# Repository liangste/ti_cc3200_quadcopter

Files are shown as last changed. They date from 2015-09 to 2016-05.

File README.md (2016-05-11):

# cc3200 quadcopter
a small quadcopter based on TI [CC3200](http://www.ti.com/product/cc3200) Wifi Processor

This is a project I started to develop a small quadcopter that I can control through my smartphone. It began as the idea: "wouldn't it be cool to fly a quadcopter with my phone?". Soon after, I got a development board for the CC3200 platform and I enrolled on a year-long journey of hw/sw development.

#Connecting to Smartphone
Connecting to Smartphone (https://youtu.be/c3Ppp-kUkaQ)

#Flight Video
Flight Video (https://youtu.be/NUO0UMu_Gpo)

Most "control" related components are routed to the top of the PCB. The board measure 4cm x 4cm and contains 4 copper layers.

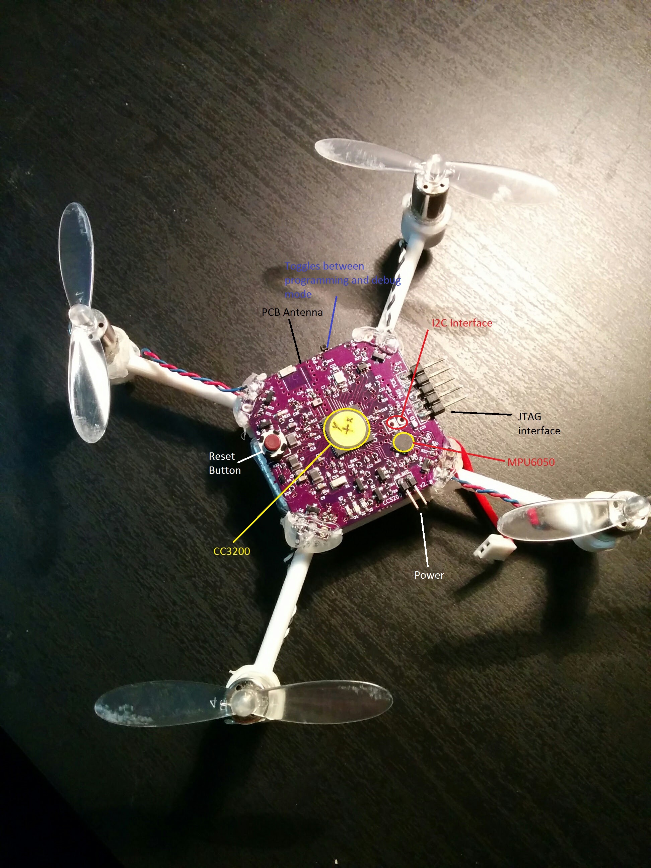
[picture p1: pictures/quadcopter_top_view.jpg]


While "Power" related components are routed to the bottom. Note that there are 4 MOSFETs placed in each corner, one for each DC motors.

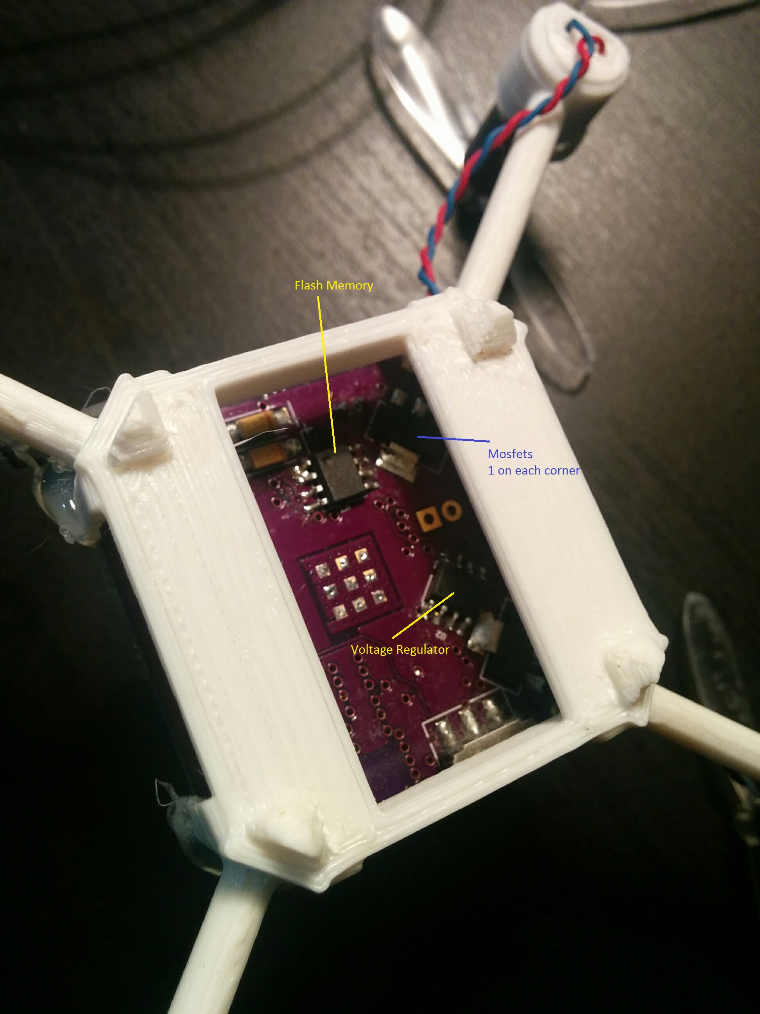
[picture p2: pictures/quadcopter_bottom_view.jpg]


While developing the sw, I also made a simple PyQt app for visualizing the measured and calculated sensor readings from the quadcopter. This "tester" app, as I call it, was important for developing Kalman filter for accelerometer and gyroscope readings.

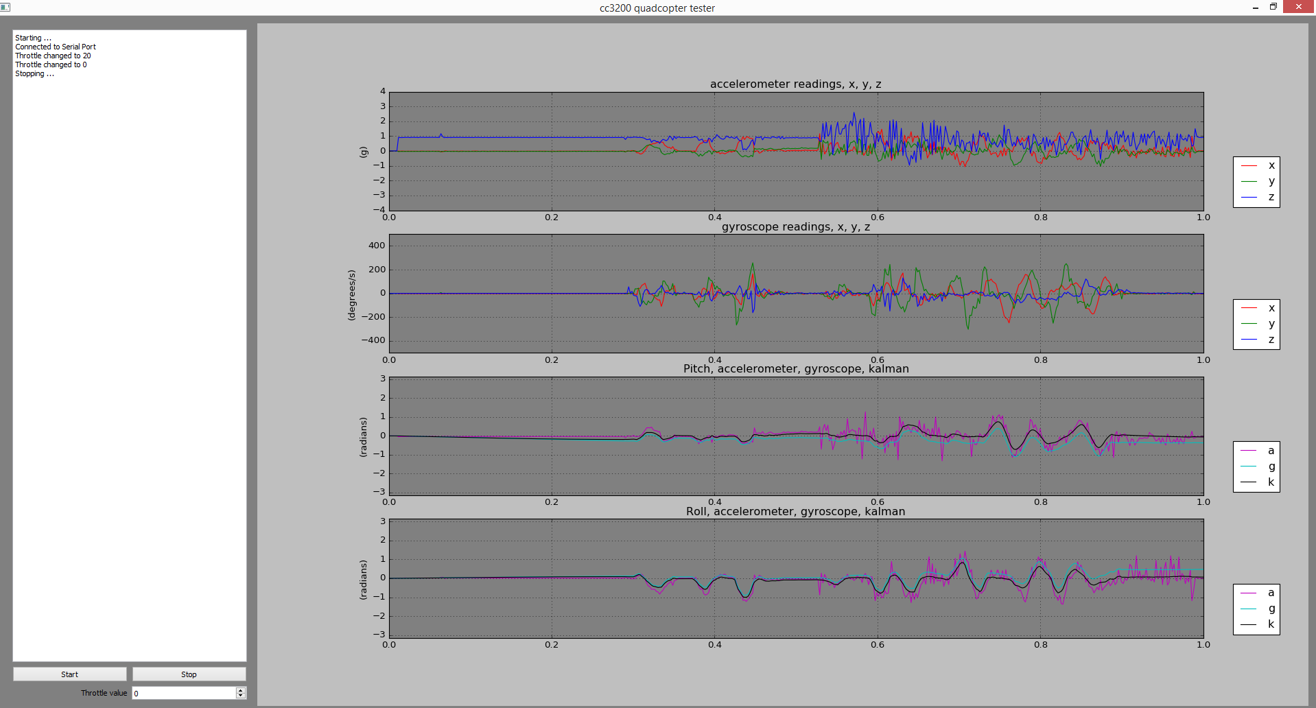
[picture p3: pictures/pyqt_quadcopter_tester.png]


Here's picture showing the "evolution" of this quadcopter. On the left we have the original CC3200 development board, on which my board designs were based. In the middle is the first version of the PCB. It was functional, but had several shortcomings that motivated me to develop another version. On the right, you see the final version with much smaller PCB mounted on a chasis that I made on SolidWorks and printed out using a local 3D printer.

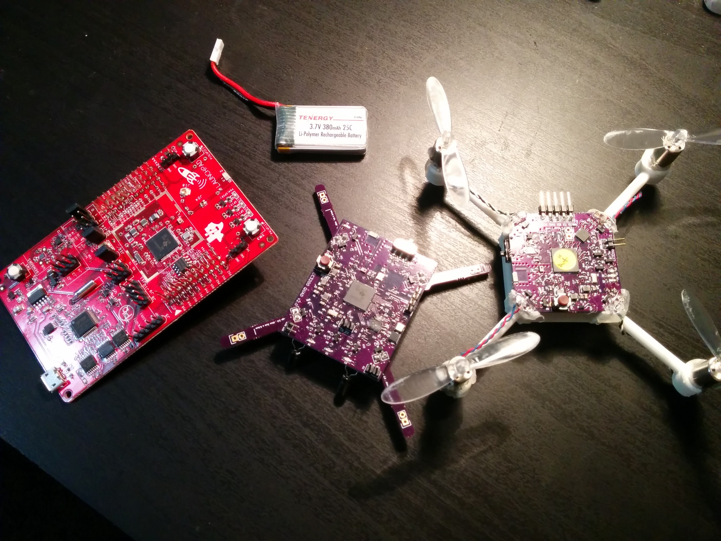
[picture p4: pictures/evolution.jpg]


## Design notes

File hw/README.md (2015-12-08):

# Hardware Overview

Photo Gallery [here](https://goo.gl/photos/aTtyzAjJARxAQHJD8)

## Introduction

The hardware is designed using [KiCAD](http://kicad-pcb.org/) and manufactured with [OSI Park](https://oshpark.com/) PCB manufacturing facility. Build version for the KiCAD used is 2014-12-04 bZR 5312.

[CC3200](http://www.ti.com/product/cc3200) is a Wifi-based microcontroller made by Texas Instruments. For this project, CC3200 is used as the processor as well as communication interface. The chip runs at 80MHz and has an embedded Wifi co-processor that I can link with and control using my smartphone. I used this chip because 1) it's not too expensive, 2) its suitable for a 4-layer design, which is the current maximum amount of layers for OSH Park and 3) because it has a Wifi co-processor in the same die.

## Hardware Breakdown

### Wifi processor

VQFN-64 package in a 9mm x 9mm package. Contains GPIO, UART, I2C, SPI, PWM, and Parallel Camera interface.

### Power

Main power source for the quad is a 3.7V Li-Po battery. The voltaged is stepped-down to 3.3V using Low-DropOut (LDO) regulators.

### Motor Control

4 MOSFETs are used to control 4 DC motors. GPIO_9, 10, 11, and 28 provide the PWM signals from CC3200.

### Acceleromter + Gyro

MPU6050 is an Gyroscope + Accelerometer 2 in 1 sensor with I2C and SPI interfaces. One nice thing about the MPU6050 is the Low-Pass Filter which can be used to filter out unwanted Acceleromter high-frequency noise caused by motor vibrations.

### Indicator LEDs

3 LEDs indicate Wifi-connectivity status, Sensor status and transmission indications. 1 Red LED is used to indicate power status.

## Build and Test

Once schematics and layouts of the board is done. The design is sent to OSH Park for processing. Turnaround time was usually 2 weeks for 2 layers boards and 3-4 weeks for 4 layer boards. Once the board arrives, I picked them up and soldered with components that I ordered separately from Digikey. I constructed a ControLeo2-based reflow oven from [Whizoo](http://www.whizoo.com/) and used it to solder SMD components on the top of the board. The bottom is left for larger components like MOSFETS, NAND memory and LDO regulators that I can solder by hand.

I used the following chart as a guide for testing each hardware components. The rows go from easiest to hardest to verify.

| Component | How to test |
| :--- | :---: |
|CC3200 Power|Is the Red Power LED on? Probe at 3.3V|
|JTAG| Use CCS to connect to CC3200 using TCK and TMS lines |
|Flash Programming| Use Tx and Rx lines to flash binaries to NAND using UniFlash |
|UART|Print out characters and receive characters from the terminal. If Flash Programming work, this should also work|
|LEDs|Blink LEDs in a sequence|
|PMW|Make sure that varying PWM duty cycle changes motor speed|
|I2C|Do a read-write-read test to scrach-pad register on MPU6050. Also test by reading its signature register|
|RF|Start a SimpleLink TCP Server and perform a packet transmission test with smartphone|

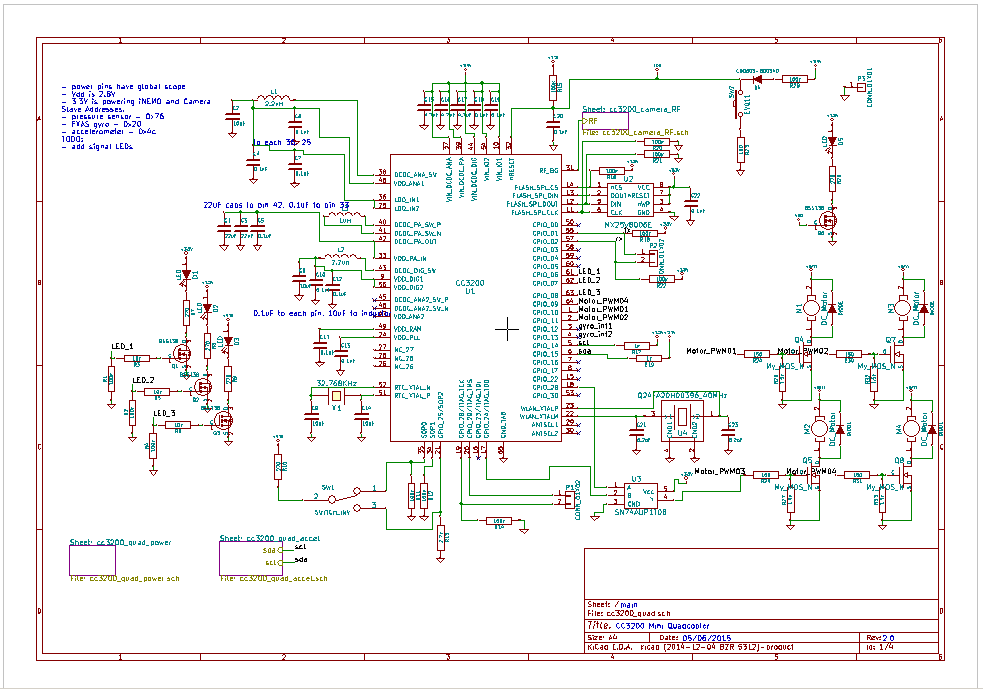
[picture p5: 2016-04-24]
pictures/schematic.png

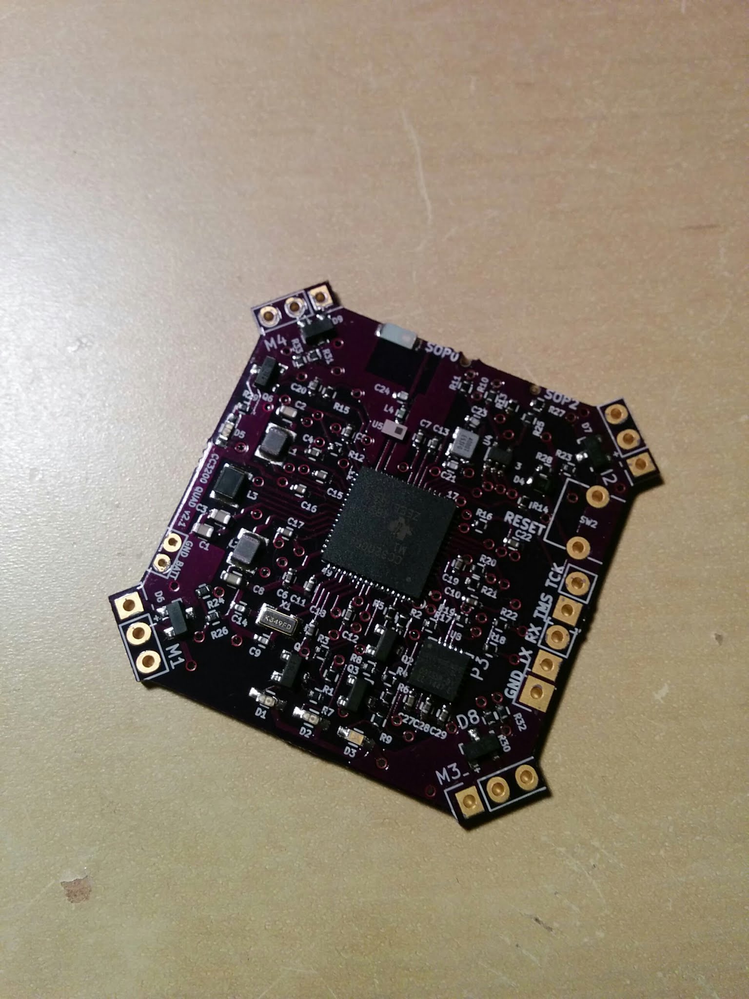
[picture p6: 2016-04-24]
pictures/after_reflow.jpg

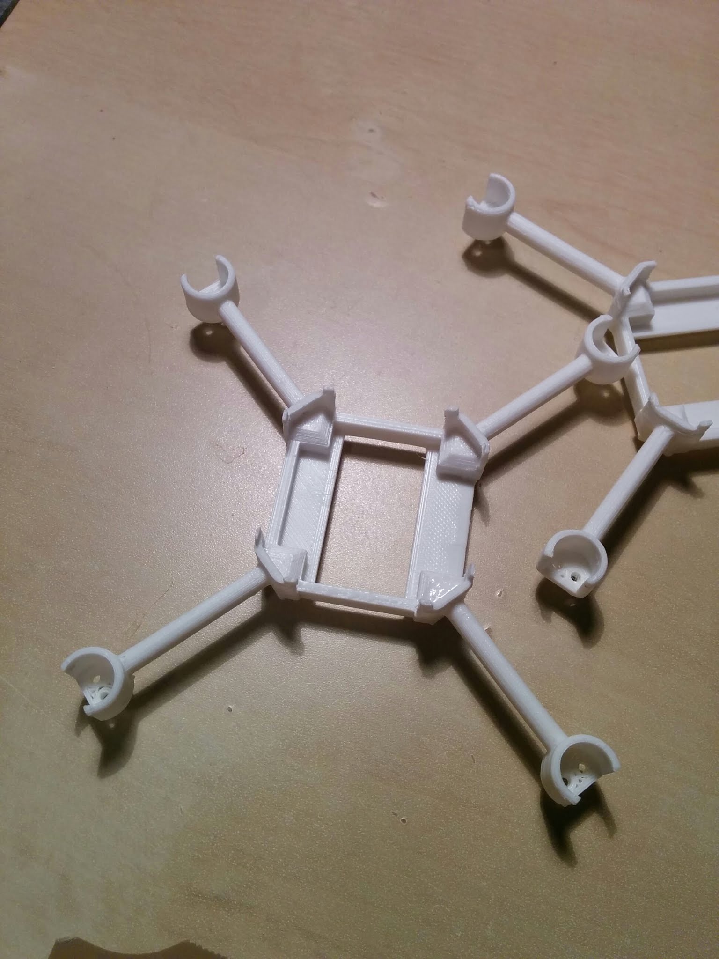
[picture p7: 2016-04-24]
pictures/quadcopter_body.jpg

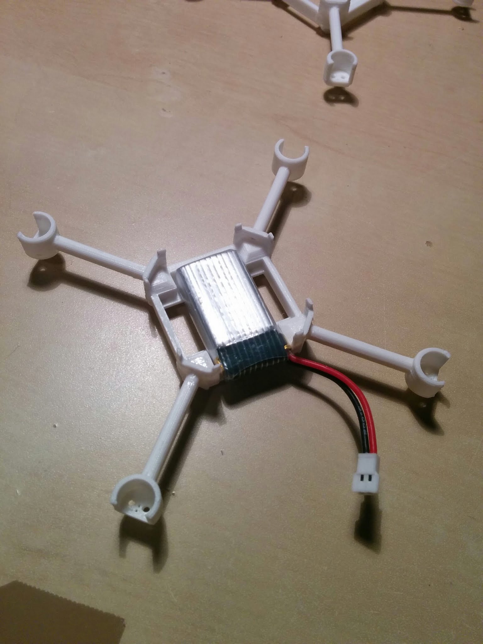
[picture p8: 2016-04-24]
pictures/quadcopter_battery_spacing.jpg

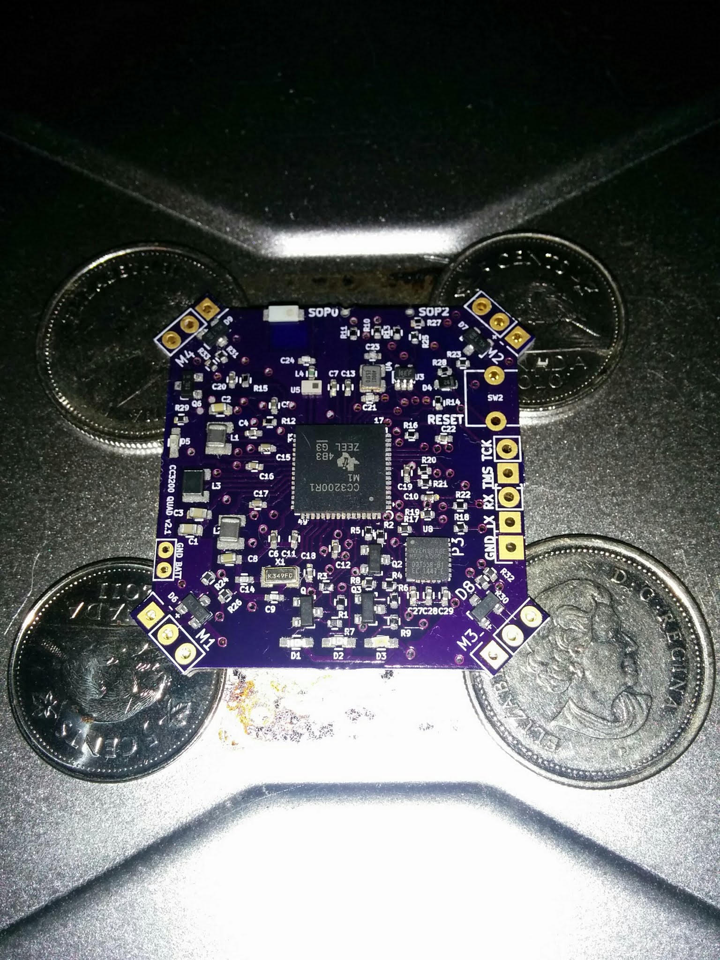
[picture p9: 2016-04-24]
pictures/reflowing.jpg

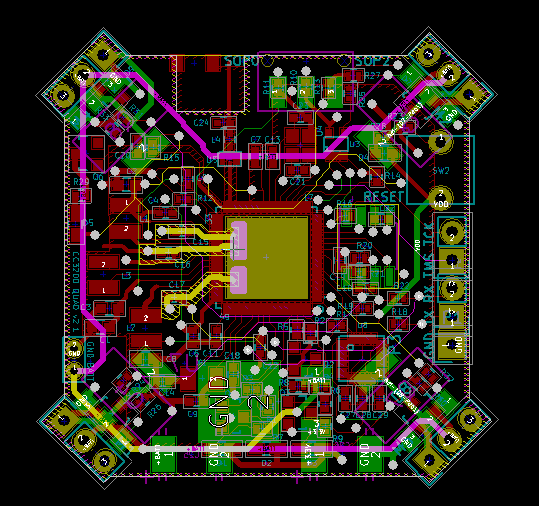
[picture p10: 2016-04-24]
pictures/pcb_layout.png

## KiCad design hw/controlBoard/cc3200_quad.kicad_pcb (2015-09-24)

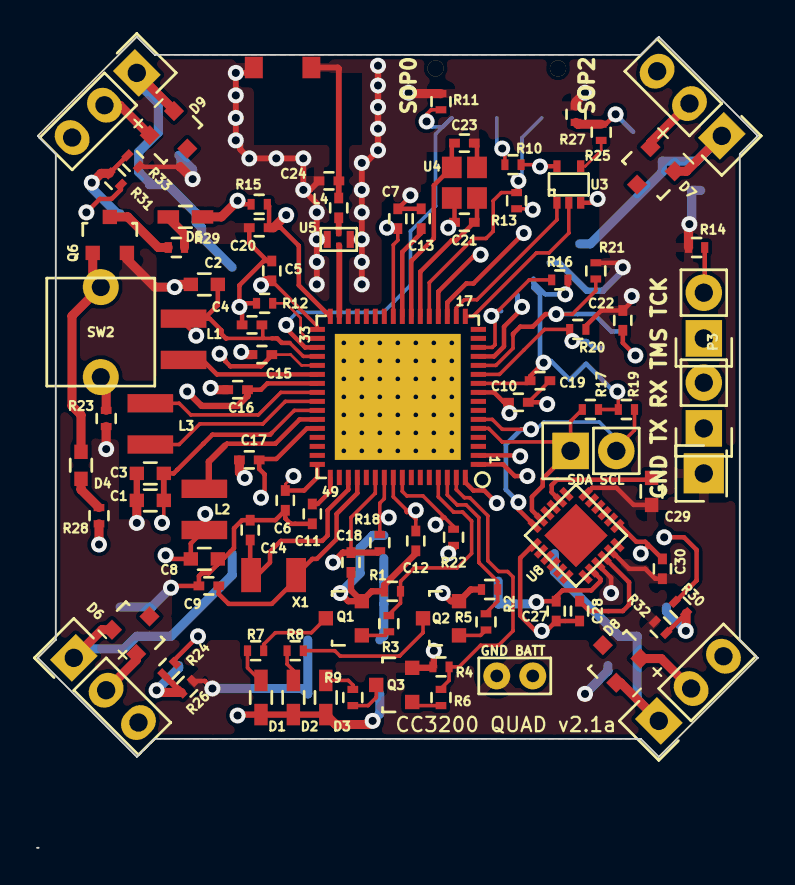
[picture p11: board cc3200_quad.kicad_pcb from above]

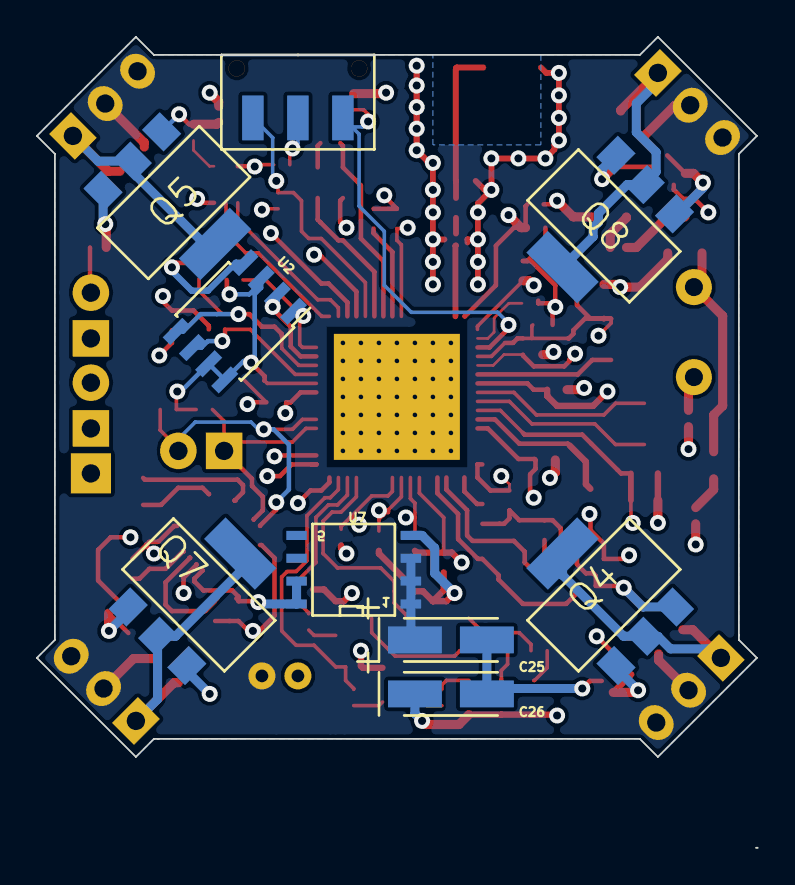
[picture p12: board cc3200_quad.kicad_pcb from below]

Board: 4 copper layers, 40.0 x 40.0 mm, 104 parts (9 on the bottom side), 65 nets.

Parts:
BT1: JST_CONNECTOR; JST_2PIN_2mm
C1, C3: 22uF; C_0603
C2, C8: 10uF; C_0603
C4, C5, C6, C7, C10, C11, C12, C13, C18, C19, C20, C22, C28, C30: 0.1uF; C_0402
C9, C14: 10pF; C_0402
C15, C16, C17: 4.7uF; C_0402
C21, C23: 6.2pF; C_0402
C24: 1.0pF; C_0402
C25, C26: 100uF; TantalC_SizeA_EIA-3216_HandSoldering
C27: 10nF; C_0402
C29: 2.2nF; C_0603
D1, D2, D3, D5: LED; C_0603_HandSoldering
D4: CD0603-B00340; C_0603
D6, D7, D8, D9: BAT54; SOT-23
L1, L2: 2.2uH; Neosid_Inductor_SM-NE29_SMD1008
L3: 1uH; Neosid_Inductor_SM-NE29_SMD1008
L4: 3.6nH; C_0402
M1, M2, M3, M4: DC_Motor; Pin_Header_Straight_1x03
P1, P2, P3: CONN_01X02; Pin_Header_Straight_1x02
P4: CONN_01X01; Pin_Header_Straight_1x01
Q1, Q2, Q3, Q6: BSS138; SOT-23
Q4, Q5, Q7, Q8: BUK9832; SOT-223
R1, R2, R4, R11, R12, R14, R15, R16, R18, R20, R21, R22, R28: 100k; R_0402
R3, R5, R6: 10k; R_0402
R7, R8, R9, R10, R29: 270; R_0402
R13: 2.7k; R_0402
R17, R19: 1k; R_0402
R23: 100; R_0402
R24, R25, R30, R31: 150; R_0402
R26, R27, R32, R33: 1.5k; R_0402
SW1: SWITCH_INV; JS102011SAQN
SW2: EVQ11; EVQ11_Push_Switch
U1: CC3200; cc3200
U2: MX25V8006E; SOIC-8_3.9x4.9mm_Pitch1.27mm
U3: SN74AUP1T08; sc70-5
U4: Q24FA20H00396_40MHz; Q24FA20H
U5: DEA202450BT-1294C1-H; DEA202450BT
U6: AH316M245001; AH316M
U7: MCP1726; SOIC-8-N
U8: MPU6050; MPU-6050
X1: 32.768KHz; ABS07

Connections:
+3.3V: C15.1, C16.1, C17.1, C18.1, C19.1, C22.1, C26.1, C27.1, C30.1, D1.1, D2.1, D3.1, D5.1, R10.1, R15.1, R16.1, R17.1, R18.1, R19.1, R22.1, R28.1, U1.10, U1.37, U1.39, U1.44, U1.54, U2.3, U2.7, U2.8, U3.5, U7.7, U7.8, U8.8, U8.13
+BATT: BT1.1, C25.1, D6.2, D7.2, D8.2, D9.2, M1.2, M2.2, M3.2, M4.2, U7.1, U7.2, U7.3
/LED_1: R1.2, R3.2, U1.61
/LED_2: R2.2, R5.2, U1.62
/LED_3: R4.2, R6.2, U1.63
/Motor_PWM01: R24.2, U1.1
/Motor_PWM02: R30.2, U1.2
/Motor_PWM03: R25.2, U3.4
/Motor_PWM04: R31.2, U1.64
/cc3200_camera_RF/RF: U1.31, U5.1
/cc3200_quad_accel/SCL: P1.1, R17.2, U1.5, U8.23
/cc3200_quad_accel/SDA: P1.2, R19.2, U1.6, U8.24
/rx: P3.2, R22.2, U1.57
/tx: P3.1, R18.2, U1.55
/~Reset: C20.1, D4.2, Q6.1, R15.2, SW2.2, U1.32
GND: BT1.2, C1.2, C2.2, C3.2, C4.2, C5.2, C6.2, C7.2, C8.2, C9.2, C10.2, C11.2, C12.2, C13.2, C14.2, C15.2, C16.2, C17.2, C18.2, C19.2, C20.2, C21.2, C22.2, C23.2, C24.1, C24.2, C25.2, C26.2, C27.2, C28.2, C29.1, C30.2, L4.2, P4.1, Q1.2, Q2.2, Q3.2, Q4.3, Q5.3, Q6.2, Q7.3, Q8.3, R1.1, R2.1, R4.1, R11.2, R12.2, R13.2, R14.1, R20.1, R21.1, R23.2, R26.1, R27.1, R32.1, R33.1, U1.65, U2.4, U3.3, U4.2, U4.4, U5.2, U5.4, U6.1, U6.2, U7.4, U8.1, U8.9, U8.11, U8.18
unnamed: C1.1, C3.1, C5.1, U1.33, U1.42
unnamed: C2.1, C4.1, C6.1, C7.1, L1.1, U1.25, U1.36, U1.48
unnamed: C9.1, U1.52, X1.2
unnamed: C8.1, C10.1, C12.1, L2.1, U1.9, U1.56
unnamed: C11.1, U1.49
unnamed: C13.1, U1.24
unnamed: C14.1, U1.51, X1.1
unnamed: C21.1, U1.22, U4.3
unnamed: C23.1, U1.23, U4.1
unnamed: C28.1, U8.10
unnamed: C29.2, U8.20
unnamed: D1.2, R7.1
unnamed: D2.2, R8.1
unnamed: D3.2, R9.1
unnamed: D4.1, R28.2
unnamed: D5.2, R29.1
unnamed: D6.1, M1.1, Q4.2
unnamed: D7.1, M2.1, Q5.2
unnamed: D8.1, M3.1, Q7.2
unnamed: D9.1, M4.1, Q8.2
unnamed: L1.2, U1.38
unnamed: L2.2, U1.43
unnamed: L3.1, U1.41
unnamed: L3.2, U1.40
unnamed: L4.1, U5.3
unnamed: P2.1, U1.20
unnamed: P2.2, R14.2, U1.19
unnamed: Q1.1, R3.1
unnamed: Q1.3, R7.2
unnamed: Q2.1, R5.1
unnamed: Q2.3, R8.2
unnamed: Q3.1, R6.1
unnamed: Q3.3, R9.2
unnamed: Q4.1, R24.1, R26.2
unnamed: Q5.1, R25.1, R27.2
unnamed: Q6.3, R29.2
unnamed: Q7.1, R30.1, R32.2
unnamed: Q8.1, R31.1, R33.2
unnamed: R10.2, SW1.2
unnamed: R11.1, SW1.1, U1.35
unnamed: R12.1, U1.34
unnamed: R13.1, SW1.3, U1.21
unnamed: R16.2, U1.14, U2.1
unnamed: R20.2, U1.11, U2.6
unnamed: R21.2, U1.12, U2.5
unnamed: R23.1, SW2.1
unnamed: U1.13, U2.2
unnamed: U1.17, U3.2
unnamed: U1.18, U3.1

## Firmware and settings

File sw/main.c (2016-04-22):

#include "config.h"

#define OSI_STACK_SIZE          524    // stack size in number of *words*
#define mainDELAY_LOOP_COUNT    100000

int init_status;
extern bool g_wifiConnected;
extern bool g_wifiDataAvailable;

extern void(* const g_pfnVectors[])(void);

static void board_init(void);

void vAssertCalled(const char *pcFile, unsigned long ulLine) {
		LOOP_FOREVER();
}

void vApplicationIdleHook(void) {
}

void vApplicationMallocFailedHook(void) {
		UART_PRINT("[Error] FreeRTOS malloc failed\r\n");
		LOOP_FOREVER();
}

void vApplicationStackOverflowHook(OsiTaskHandle *pxTask,
				signed char *pcTaskName) {
		UART_PRINT("[Error] FreeRTOS stack overflow\r\n");
		LOOP_FOREVER();
}

static void board_init(void) {
		MAP_IntVTableBaseSet((unsigned long)&g_pfnVectors[0]);

		MAP_IntMasterEnable();
		MAP_IntEnable(FAULT_SYSTICK);

		PRCMCC3200MCUInit();
}

// ORANGE Blinking LED
void WifiIndicatorTask(void *pvParameters) {
		while(1)
		{
				wifi_indicator_ticks++;
				if (g_wifiInitialized)
				{
						if (g_wifiConnected)
								led_set(ORANGE);
						else
								led_toggle(ORANGE);
				}
				vTaskDelay(100);
		}
}

// GREEN Blinking LED
void SensorIndicatorTask(void *pvParameters) {
		while(1)
		{
				/*
				sensor_indicator_ticks++;
				if (g_sensorInitialized)
				{
						if (g_sensorConnected)
								led_toggle(GREEN);
						g_sensorConnected = 0;
				}
				*/
				vTaskDelay(1000);
		}
}

// BLUE Blinking LED
void CommIndicatorTask(void *pvParameters) {
		while(1)
		{
				comm_indicator_ticks++;
				if (g_wifiConnected) {
						led_toggle(BLUE);
						g_wifiConnected = 0;
				}
				else
						led_clear(BLUE);
				vTaskDelay(40);
		}
}

int main()
{
		board_init();
		pinmux_config();
		InitTerm();

		UART_PRINT("========================================\r\n");
		UART_PRINT("   Initializing CC3200 Quad Firmware\r\n");
		UART_PRINT("========================================\r\n");

		init_status = 0;
		g_wifiConnected = false;
		motors_init();
		led_init();
		if (!mpu6050_init(&init_status)) {
			FAIL("Failed to initialize MPU 6050 Sensor");
			goto LOOP_FOREVER;
		}

		wifiDataLock = xSemaphoreCreateMutex();
		g_wifiDataAvailable = false;

		VStartSimpleLinkSpawnTask(SPAWN_TASK_PRIORITY);

		//xTaskCreate(SerialControlTask, NULL, OSI_STACK_SIZE, (void *) NULL, 5, NULL);
		xTaskCreate(StabilizerTask, NULL, OSI_STACK_SIZE, (void *) NULL, 5, NULL);
		xTaskCreate(WifiConnectTask, NULL, OSI_STACK_SIZE, (void *) NULL, 5, NULL);

		INFO("Starting FreeRTOS Scheduling");
		vTaskStartScheduler();

LOOP_FOREVER:
		led_set(BLUE);
		motors_set_m1(0);
		motors_set_m2(0);
		motors_set_m3(0);
		motors_set_m4(0);
		while(1) {};
		return 0;
}

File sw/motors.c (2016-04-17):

#include "config.h"
#include "stdint.h"

void _update_duty_cycle(
    unsigned long ulBase,
    unsigned long ulTimer,
    uint8_t ucLevel)
{
    //
    // Match value is updated to reflect the new dutycycle settings
    //
    MAP_TimerMatchSet(ulBase,ulTimer,(ucLevel*DUTYCYCLE_GRANULARITY));
}

void _setup_timer_pwm_mode(
    unsigned long ulBase,
    unsigned long ulTimer,
    unsigned long ulConfig,
    unsigned char ucInvert)
{
    //
    // Set GPT - Configured Timer in PWM mode.
    //
    MAP_TimerConfigure(ulBase, ulConfig);
    MAP_TimerPrescaleSet(ulBase, ulTimer, 0);

    //
    // Inverting the timer output if required
    //
    MAP_TimerControlLevel(ulBase, ulTimer, ucInvert);

    //
    // Load value set to ~0.5 ms time period
    //
    MAP_TimerLoadSet(ulBase,ulTimer,TIMER_INTERVAL_RELOAD);

    //
    // Match value set so as to output level 0
    //
    MAP_TimerMatchSet(ulBase,ulTimer,TIMER_INTERVAL_RELOAD);

}

void motors_init() {
    MAP_PRCMPeripheralClkEnable(PRCM_TIMERA0, PRCM_RUN_MODE_CLK); // m3
    MAP_PRCMPeripheralClkEnable(PRCM_TIMERA2, PRCM_RUN_MODE_CLK); // m4
    MAP_PRCMPeripheralClkEnable(PRCM_TIMERA3, PRCM_RUN_MODE_CLK); // m1 & m2

    _setup_timer_pwm_mode(TIMERA0_BASE, TIMER_A,
            (TIMER_CFG_SPLIT_PAIR | TIMER_CFG_A_PWM), 1);

    _setup_timer_pwm_mode(TIMERA2_BASE, TIMER_B,
            (TIMER_CFG_SPLIT_PAIR | TIMER_CFG_B_PWM), 1);

    _setup_timer_pwm_mode(TIMERA3_BASE, TIMER_A,
            (TIMER_CFG_SPLIT_PAIR | TIMER_CFG_A_PWM | TIMER_CFG_B_PWM), 1);

    _setup_timer_pwm_mode(TIMERA3_BASE, TIMER_B,
            (TIMER_CFG_SPLIT_PAIR | TIMER_CFG_A_PWM | TIMER_CFG_B_PWM), 1);

    MAP_TimerEnable(TIMERA0_BASE,TIMER_A);
    MAP_TimerEnable(TIMERA2_BASE,TIMER_B);
    MAP_TimerEnable(TIMERA3_BASE,TIMER_A);
    MAP_TimerEnable(TIMERA3_BASE,TIMER_B);

    MAP_GPIOPinWrite(GPIOA3_BASE, GPIO_PIN_4, GPIO_PIN_4); // enable AND-gate bypass

    motors_set_m1(0);
    motors_set_m2(0);
    motors_set_m3(0);
    motors_set_m4(0);
}

uint8_t motors_correct_throttle(int32_t throttle)
{
    if (throttle > MAX_THROTTLE_VALUE) {
        return MAX_THROTTLE_VALUE;
    } else if (throttle < MIN_THROTTLE_VALUE) {
        return MIN_THROTTLE_VALUE;
    }
    return (uint8_t) throttle;
}

void motors_set_m1(uint8_t val) {
    _update_duty_cycle(TIMERA3_BASE, TIMER_A, val);
}

void motors_set_m2(uint8_t val) {
    _update_duty_cycle(TIMERA0_BASE, TIMER_A, val);
}

void motors_set_m3(uint8_t val) {
    _update_duty_cycle(TIMERA3_BASE, TIMER_B, val);
}

void motors_set_m4(uint8_t val) {
    _update_duty_cycle(TIMERA2_BASE, TIMER_B, val);
}

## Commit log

2015-09-24 hw project from bitbucket
    [cc3200_camera_RF.sch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]
2015-12-15 XBox360 Controller Driver stub
2016-01-26 Qt-based Quadcopter ui application to help develop quadcopter sw
    [cube.obj, cube_x.obj, quad_assem.obj]
2016-04-07 new mpu6050 call to get sensor values
2016-04-10 throttle-handling from tester.py
2016-04-10 pitch and row angle canculation and display on tester.py
2016-04-16 Kalman Filter Implementation
2016-04-17 initial PID implementation, still need to get tuned and tested
2016-04-18 PID tuning, now the Quadcopter can hover!!!
2016-04-20 PID tuning and Yaw PID implementation. My quadcopter stopped spinning and can basically hover, but still a little shaky.
    When not shaking, the quad tend to drift to motor 1, next stop I should implement pitch & roll control so I can stop this drifting from my side
    [stabilizer.c]
2016-04-21 Roll and Pitch control and more PID tuning
2016-04-21 PID tuning again and direct throttle control (which improved handling)
2016-04-22 PID tuning update
2016-04-24 deleting Qt project and added a picture gallery folder
    [cube.obj, cube_x.obj, quad_assem.obj]
